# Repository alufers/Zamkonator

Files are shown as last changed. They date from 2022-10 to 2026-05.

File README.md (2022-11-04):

# Zamkonator - a PoE powered electronic lock system

**INFO**: This project is in a work in progress state and is not yet complete.

This is a repository for the hardware and software for a PoE powered locks system. It reads RFID cards using the [Wiegand interface](https://en.wikipedia.org/wiki/Wiegand_interface), and opens an electronic door latch to grant entry. This project simplifies the deployment of such systems by eliminating the need for a separate power supply for the lock. Additionally it connects directly to a LDAP server to authenticate users, thus removing any central coordination between multiple locks.

## Hardware overview

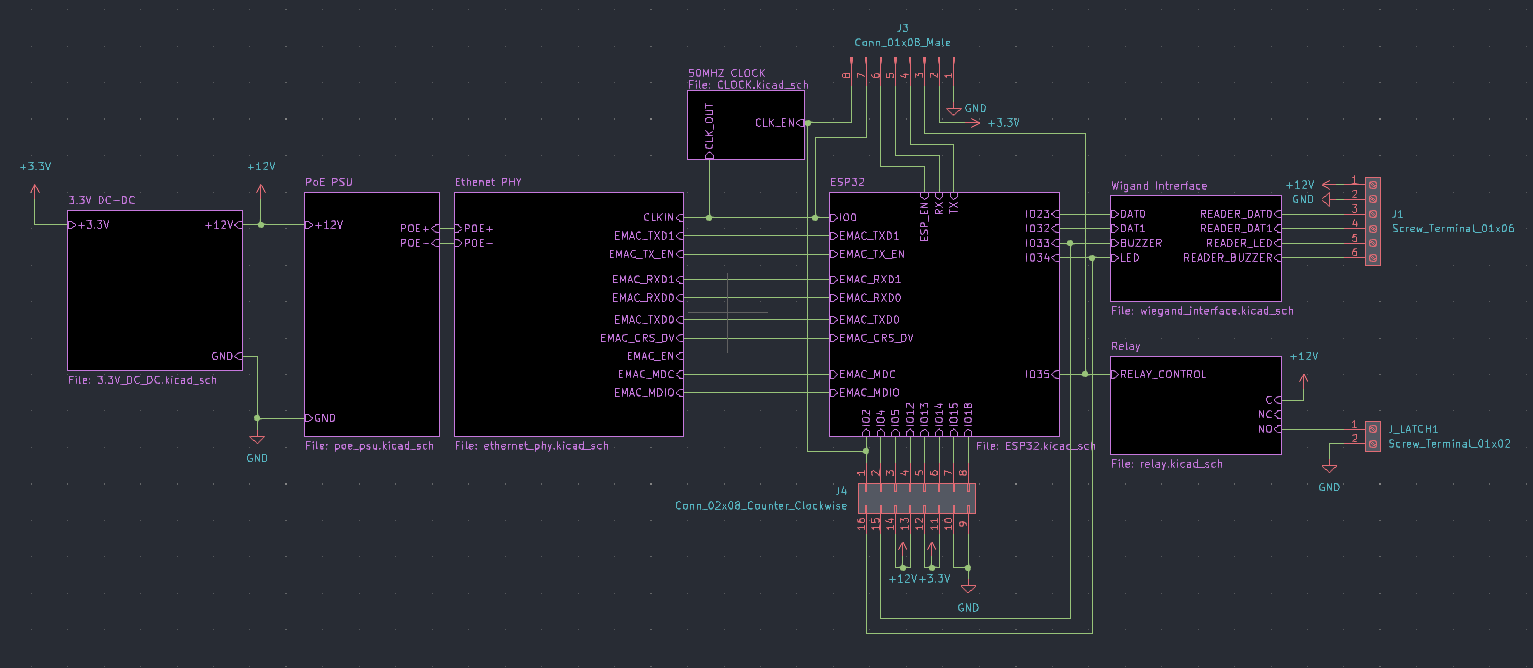
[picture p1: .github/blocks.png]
Hardware overview


The system is based on the ESP32 SoC and the RTL8201F PHY. The PoE power supply is supplied by the [SI3404-A-GM](https://datasheet.lcsc.com/lcsc/2108241830_SILICON-LABS-SI3404-A-GMR_C461934.pdf) IC. To provide an extra layer of safety, the Wiegand interface is isolated using optocouplers and the lock is controlled via a relay to eliminate any possibility of surges occuring in long cables.

[Full PDF schematic](./schematic.pdf)

## Firmware

The firmware is located in the `zamek-firmware/` directory. To build it you will need ESP-IDF 4.4.2.

### Building

```sh
# with the ESP-IDF activated, in the zamek-firmware/ directory
idf.py build
```

Alternatively you can use included nix shell, which automatically downloads and activates the ESP-IDF.

```sh
nix develop
idf.py build
```

### Flashing

```sh
# with the ESP-IDF activated
idf.py flash
```

If you are flashing a board for the first time you will also need to flash the littlefs partition. To do that run:

```sh
./flash_littlefs.sh
```

# License

MIT

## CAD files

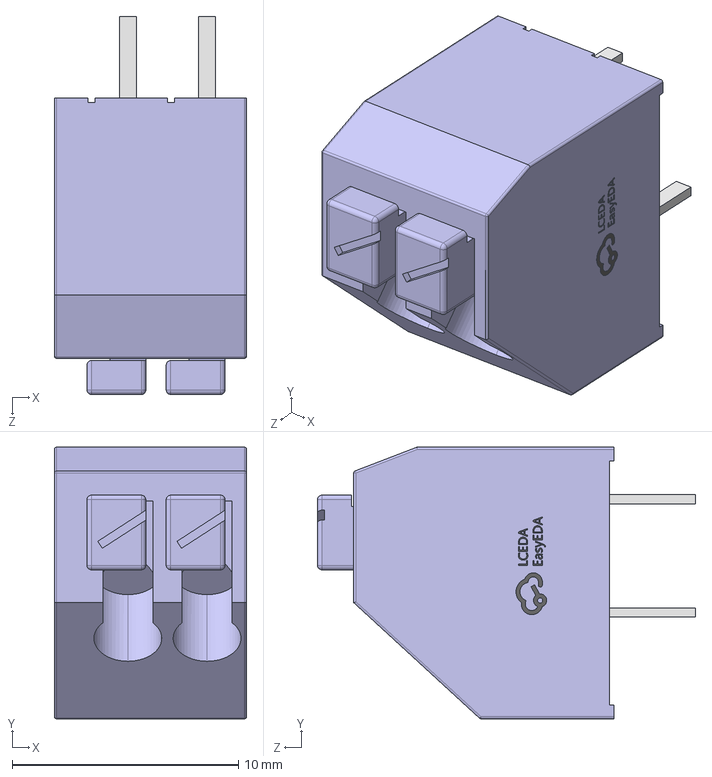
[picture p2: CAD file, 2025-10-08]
3d_models/CONN-TH_250-202.step
8.50 x 12.0 x 16.7 mm

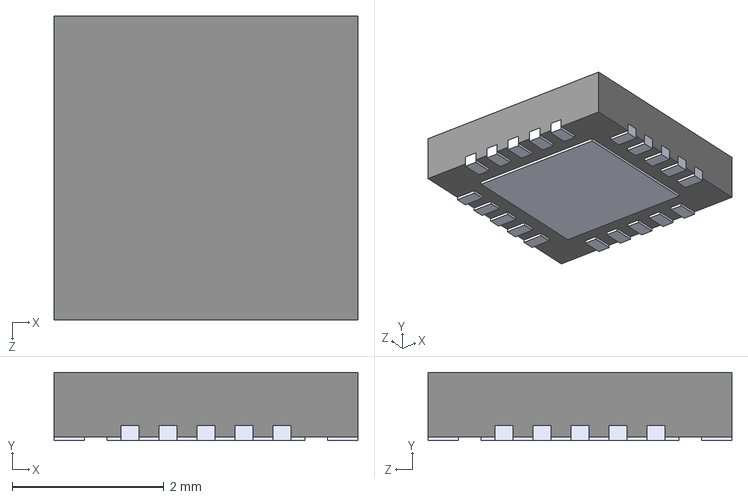
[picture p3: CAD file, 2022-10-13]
SI3404-A-GM.step
4.00 x 0.9 x 4.00 mm

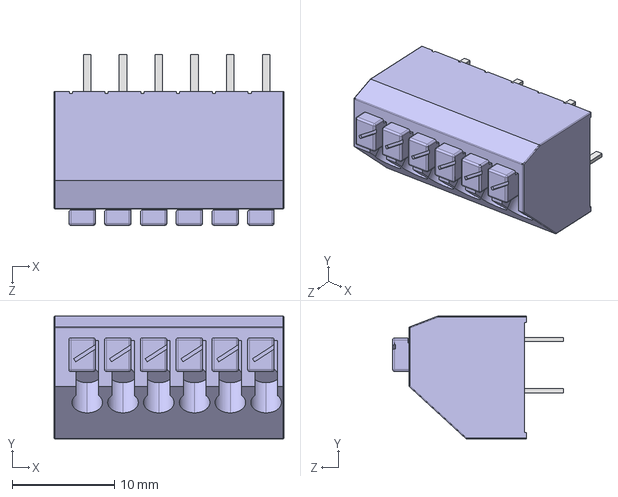
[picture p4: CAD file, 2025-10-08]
3d_models/CONN-TH_250-206.step
22.5 x 12.0 x 16.7 mm

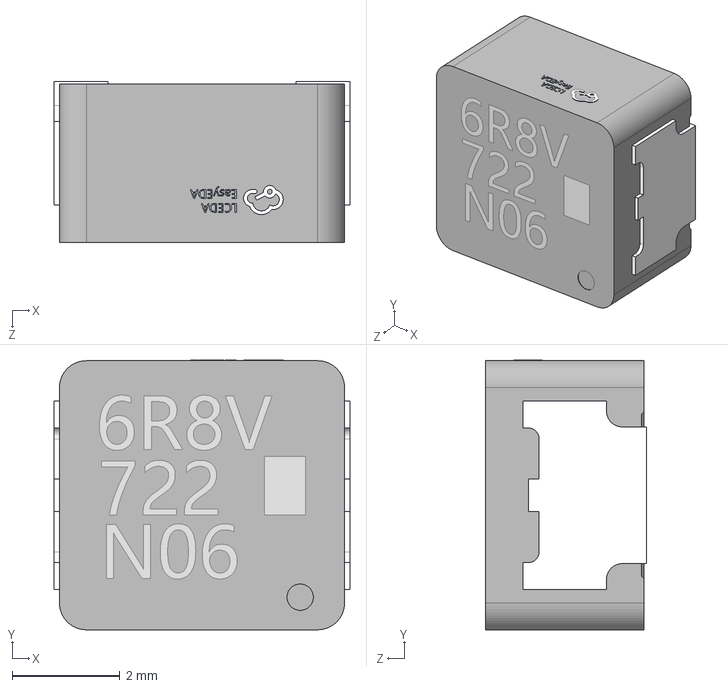
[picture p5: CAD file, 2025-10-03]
3d_models/IND-SMD_L5.5-W5.0-H3.0_ETQP4M220YFP.step
5.50 x 5.01 x 3.00 mm

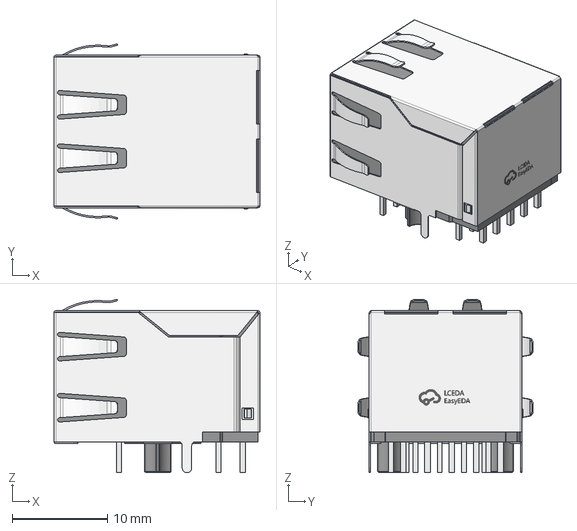
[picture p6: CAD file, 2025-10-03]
3d_models/RJ45-TH_HY931147C.step
21.6 x 18.4 x 18.2 mm

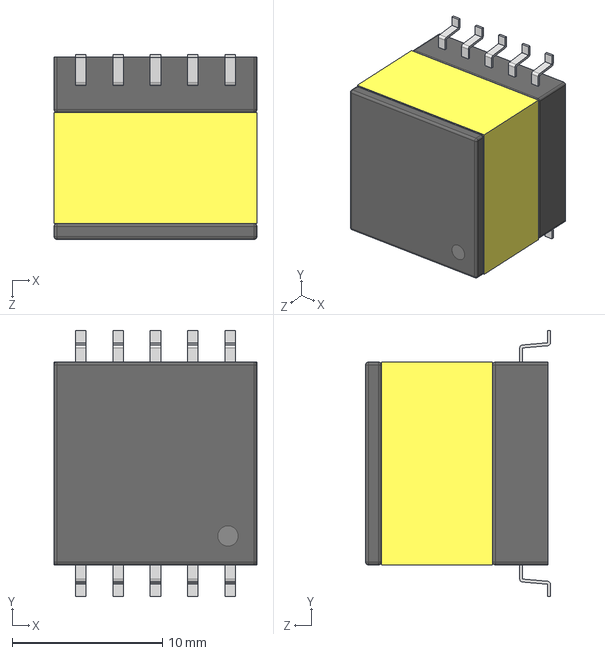
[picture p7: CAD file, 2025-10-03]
3d_models/XFMR-SMD_10P-L13.5-W13.5-H12.3-P2.48-LS17.7-BR.step
13.5 x 17.7 x 12.3 mm

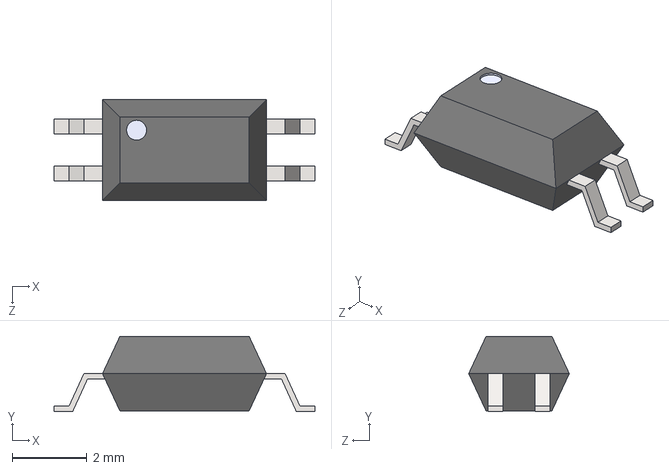
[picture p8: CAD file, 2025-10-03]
3d_models/SSOP-4.STEP
7.00 x 2.02 x 2.70 mm

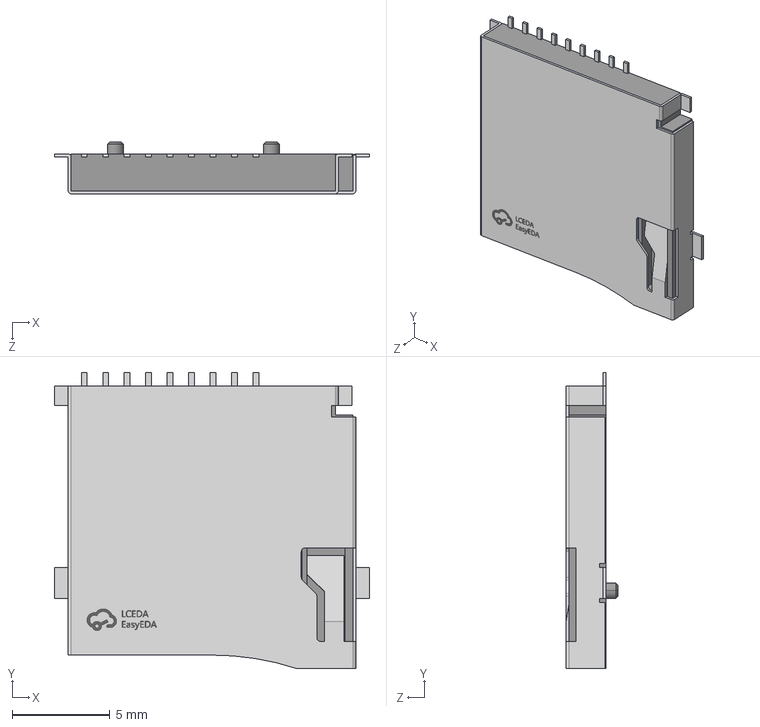
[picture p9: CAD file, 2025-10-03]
3d_models/TF-SMD_XKTF-N02-N.step
16.1 x 15.2 x 2.65 mm

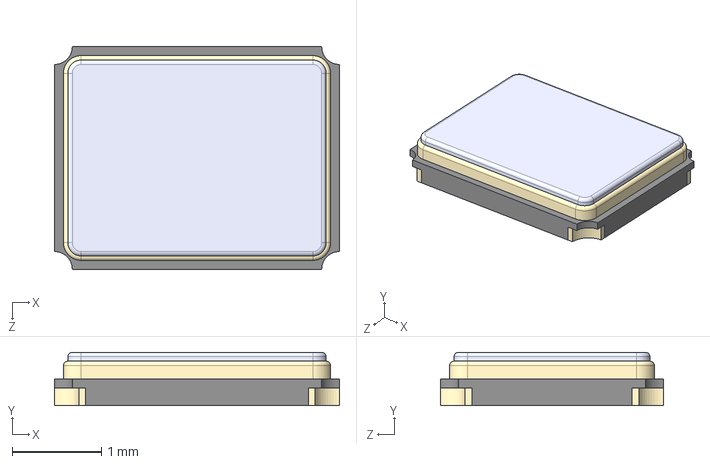
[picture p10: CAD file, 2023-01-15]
3d_models/Oscillator_3225.step
3.20 x 0.6 x 2.50 mm

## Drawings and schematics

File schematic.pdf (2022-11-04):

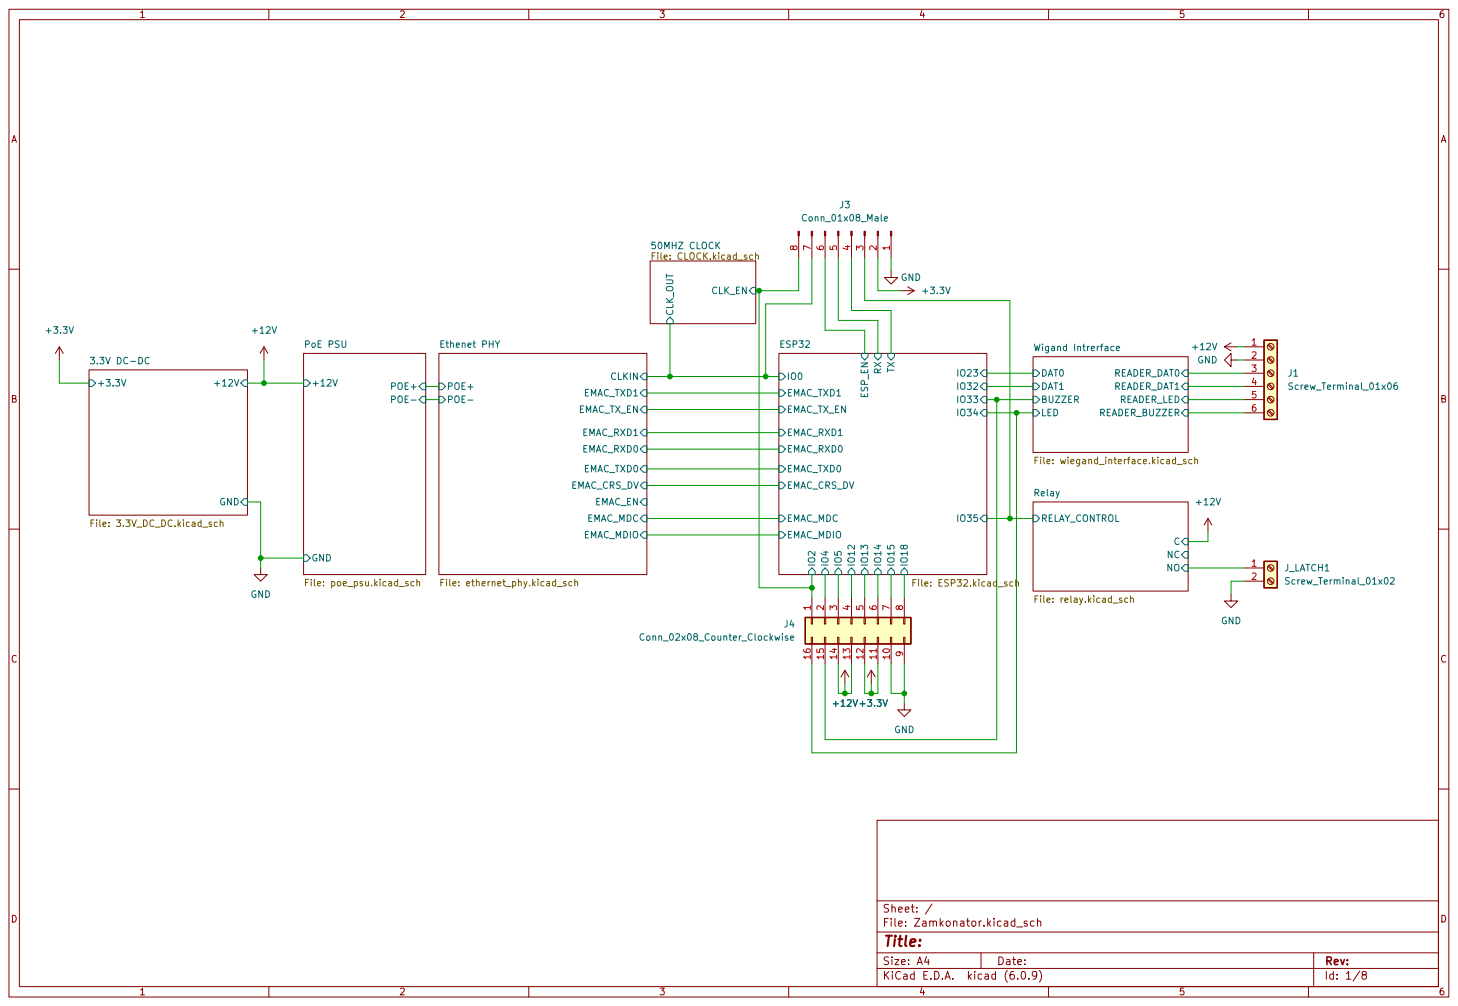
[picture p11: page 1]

POE+ POE- PoE PSU

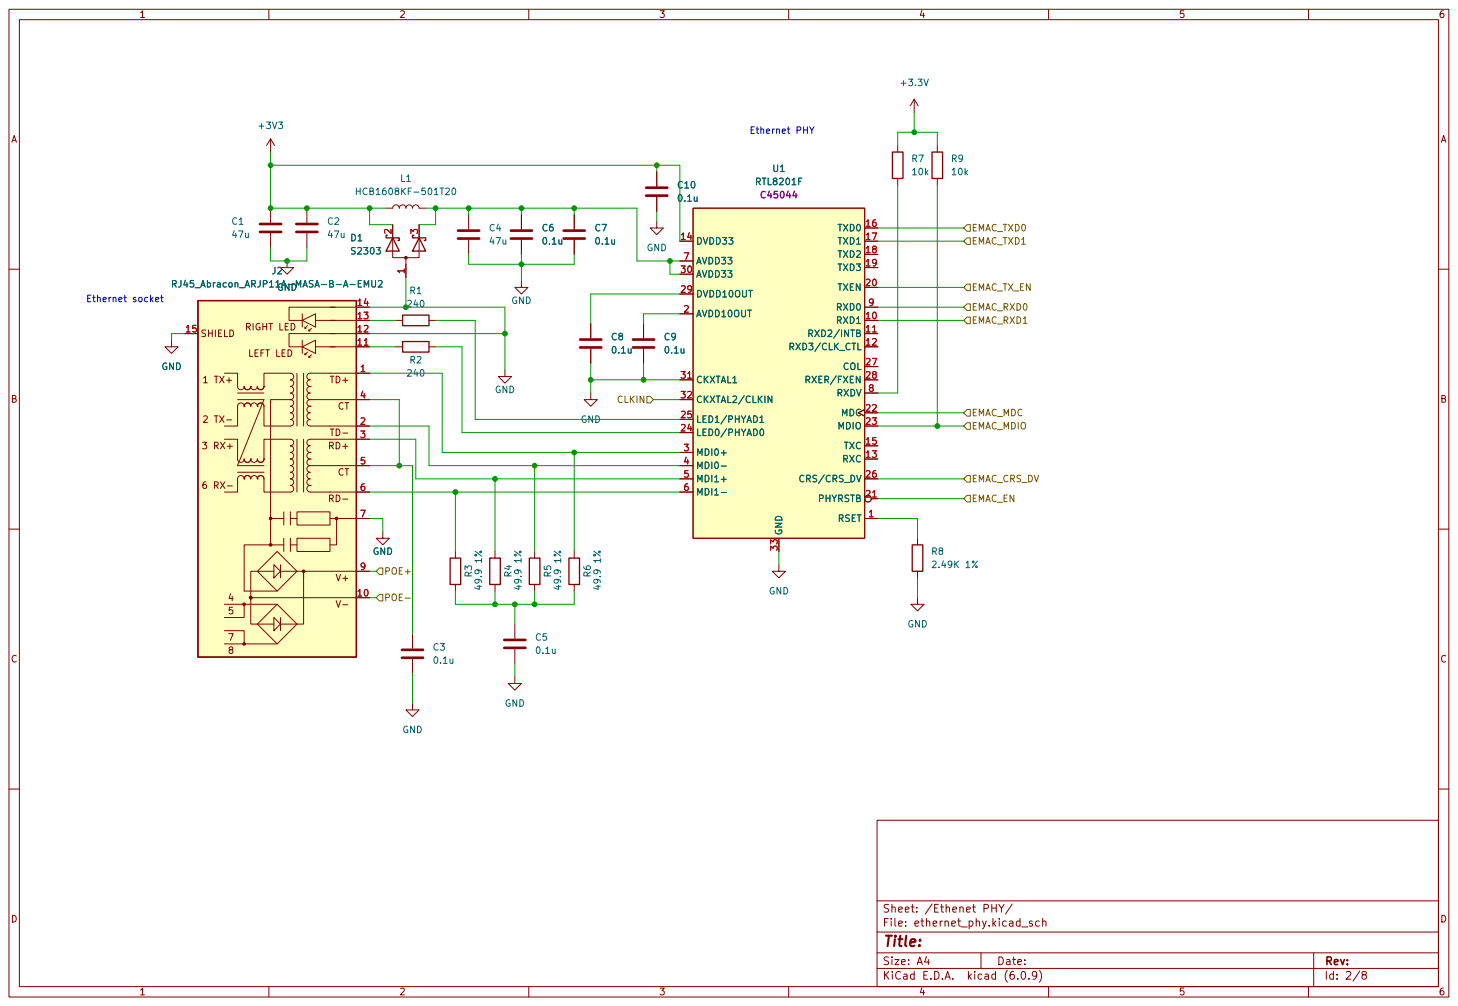
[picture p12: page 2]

Ethernet PHY
V+V- CT RD+ RIGHT LED

File: ethernet_phy.kicad_sch Sheet: /Ethenet PHY/
Id: 2/8 Title:

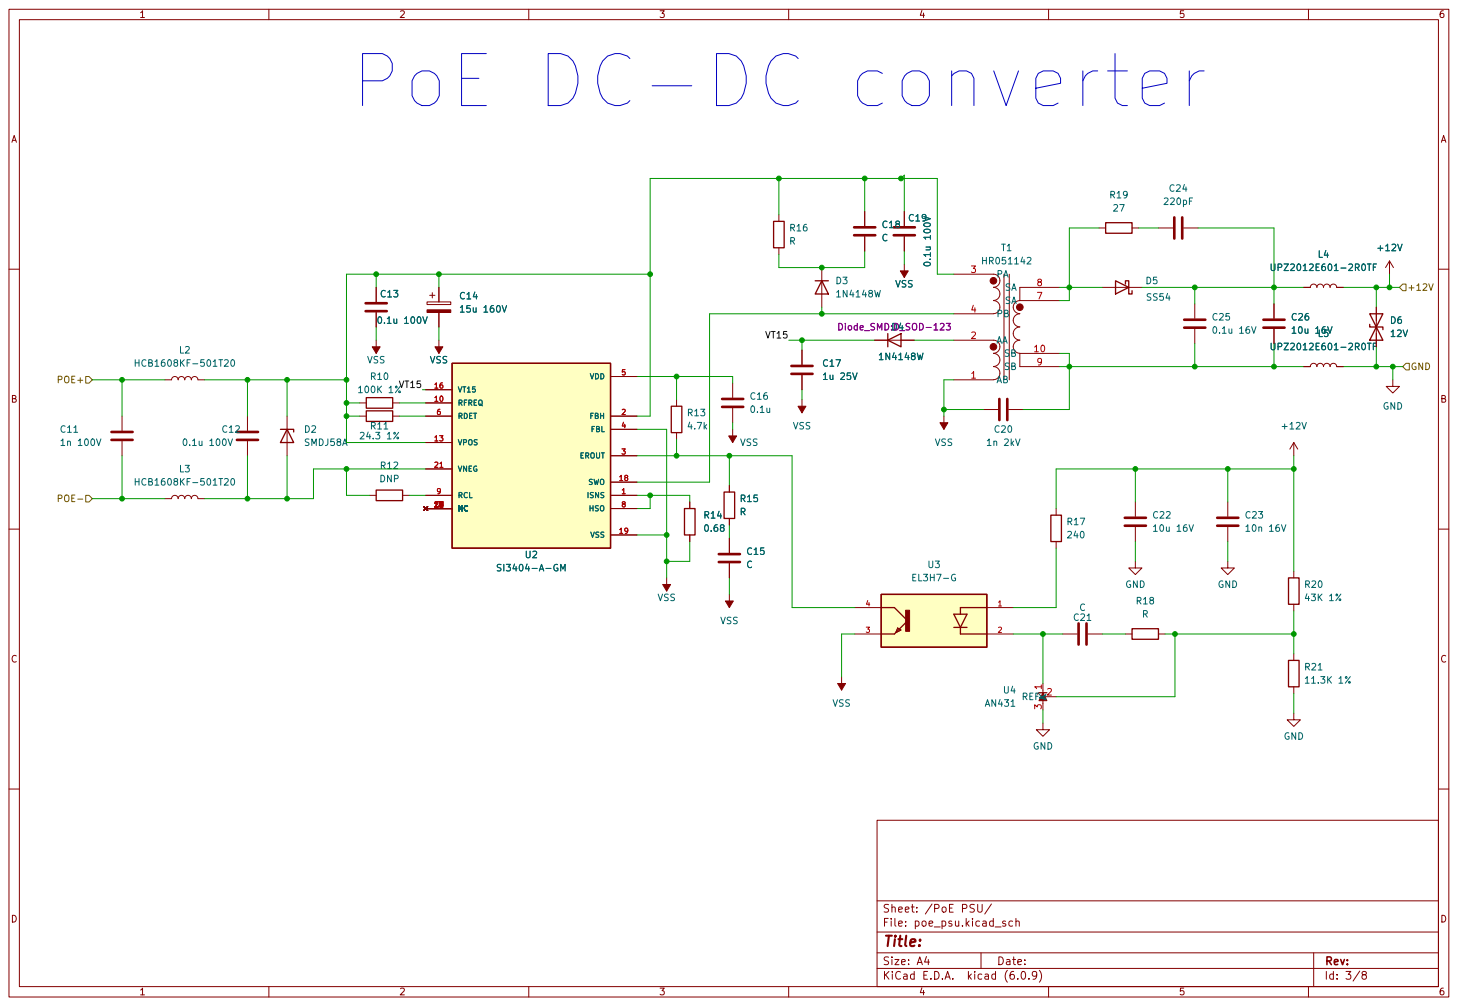
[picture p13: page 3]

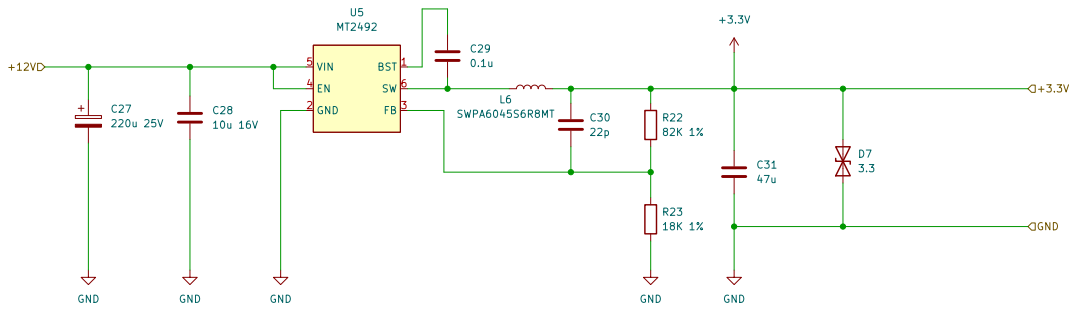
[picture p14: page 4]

File: 3.3V_DC_DC.kicad_sch Sheet: /3.3V DC-DC/
Id: 4/8 Title:

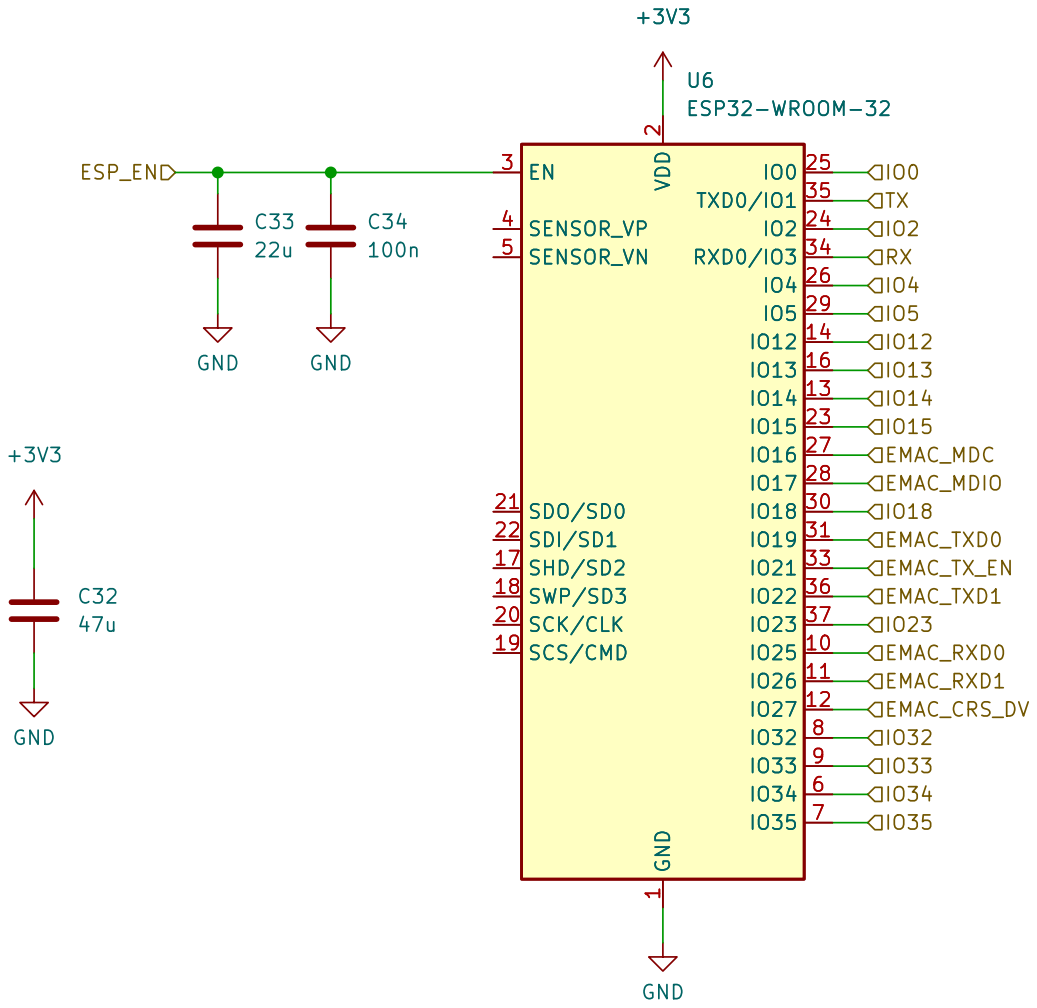
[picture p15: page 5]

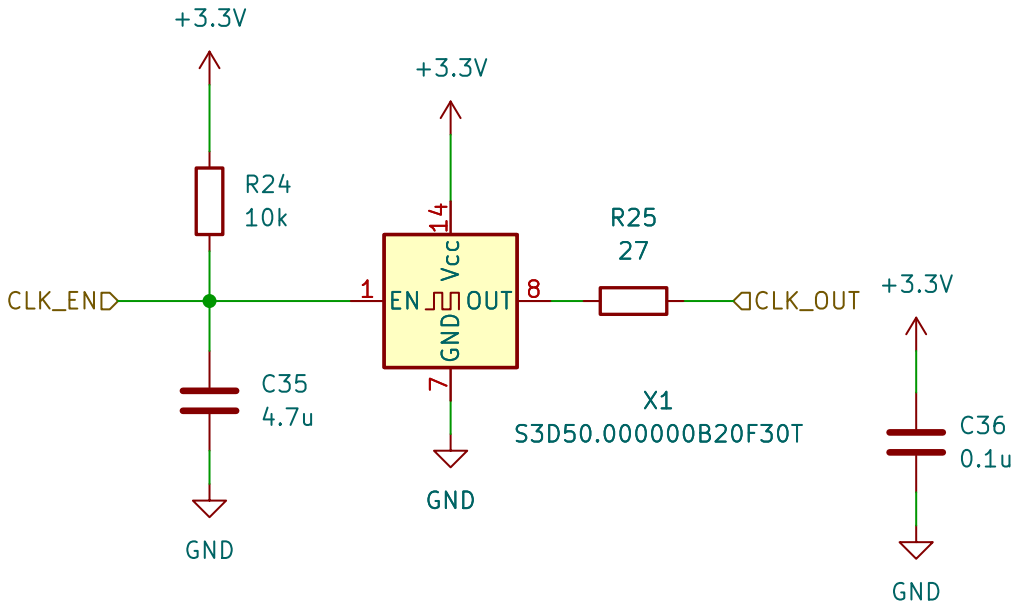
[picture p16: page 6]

File: CLOCK.kicad_sch Sheet: /50MHZ CLOCK/
Id: 6/8 Title:

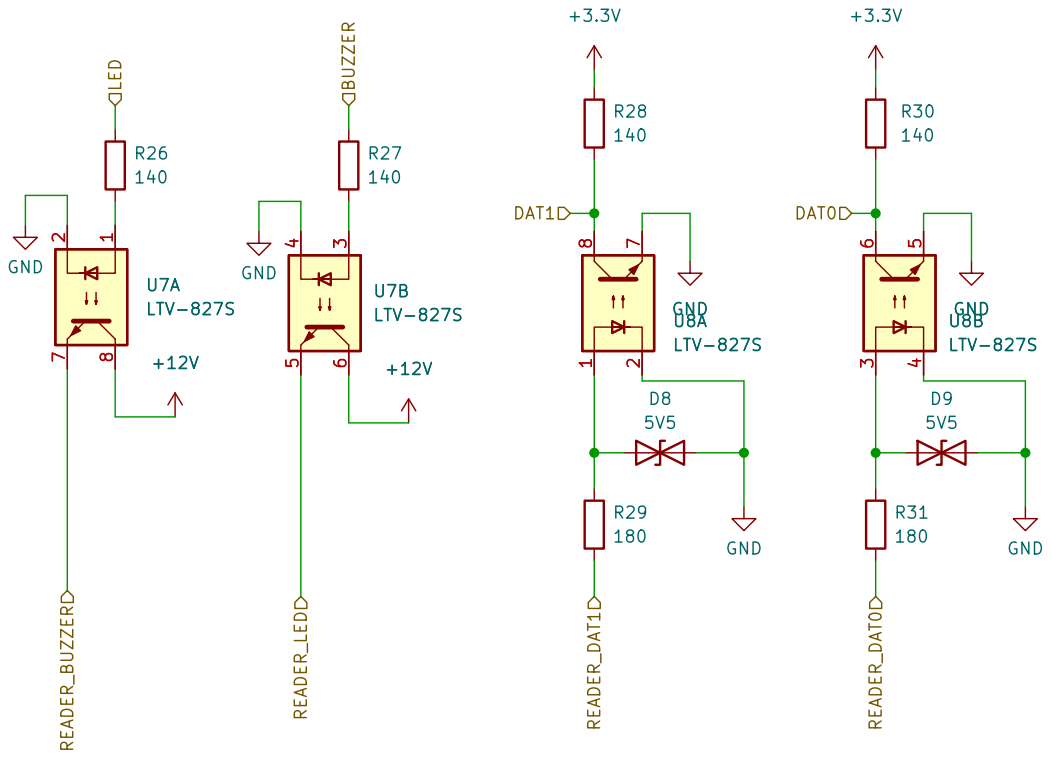
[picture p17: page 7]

Sheet: /Wigand Intrerface/ GND

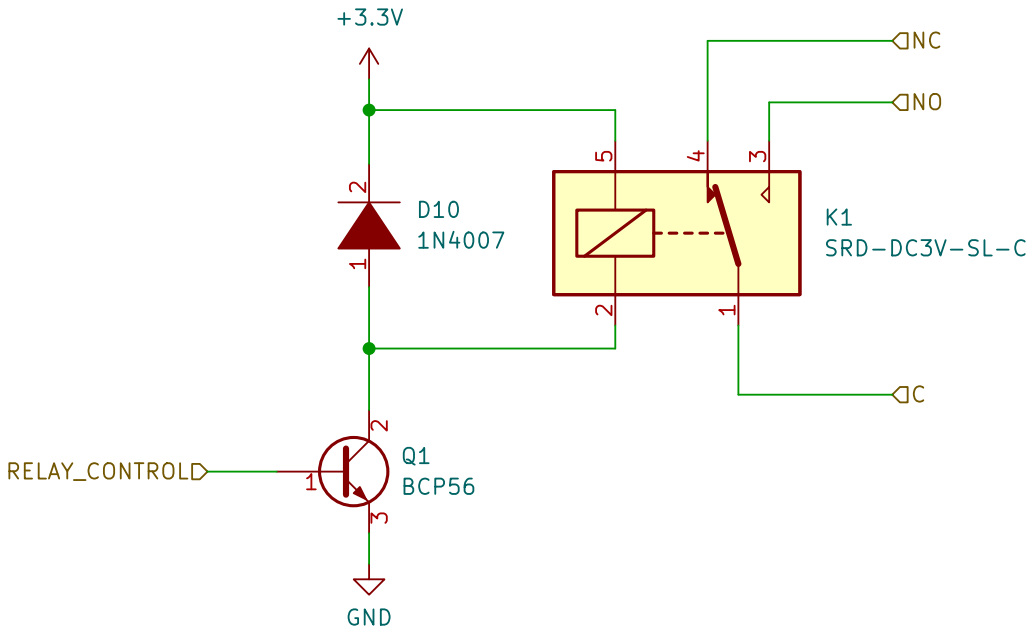
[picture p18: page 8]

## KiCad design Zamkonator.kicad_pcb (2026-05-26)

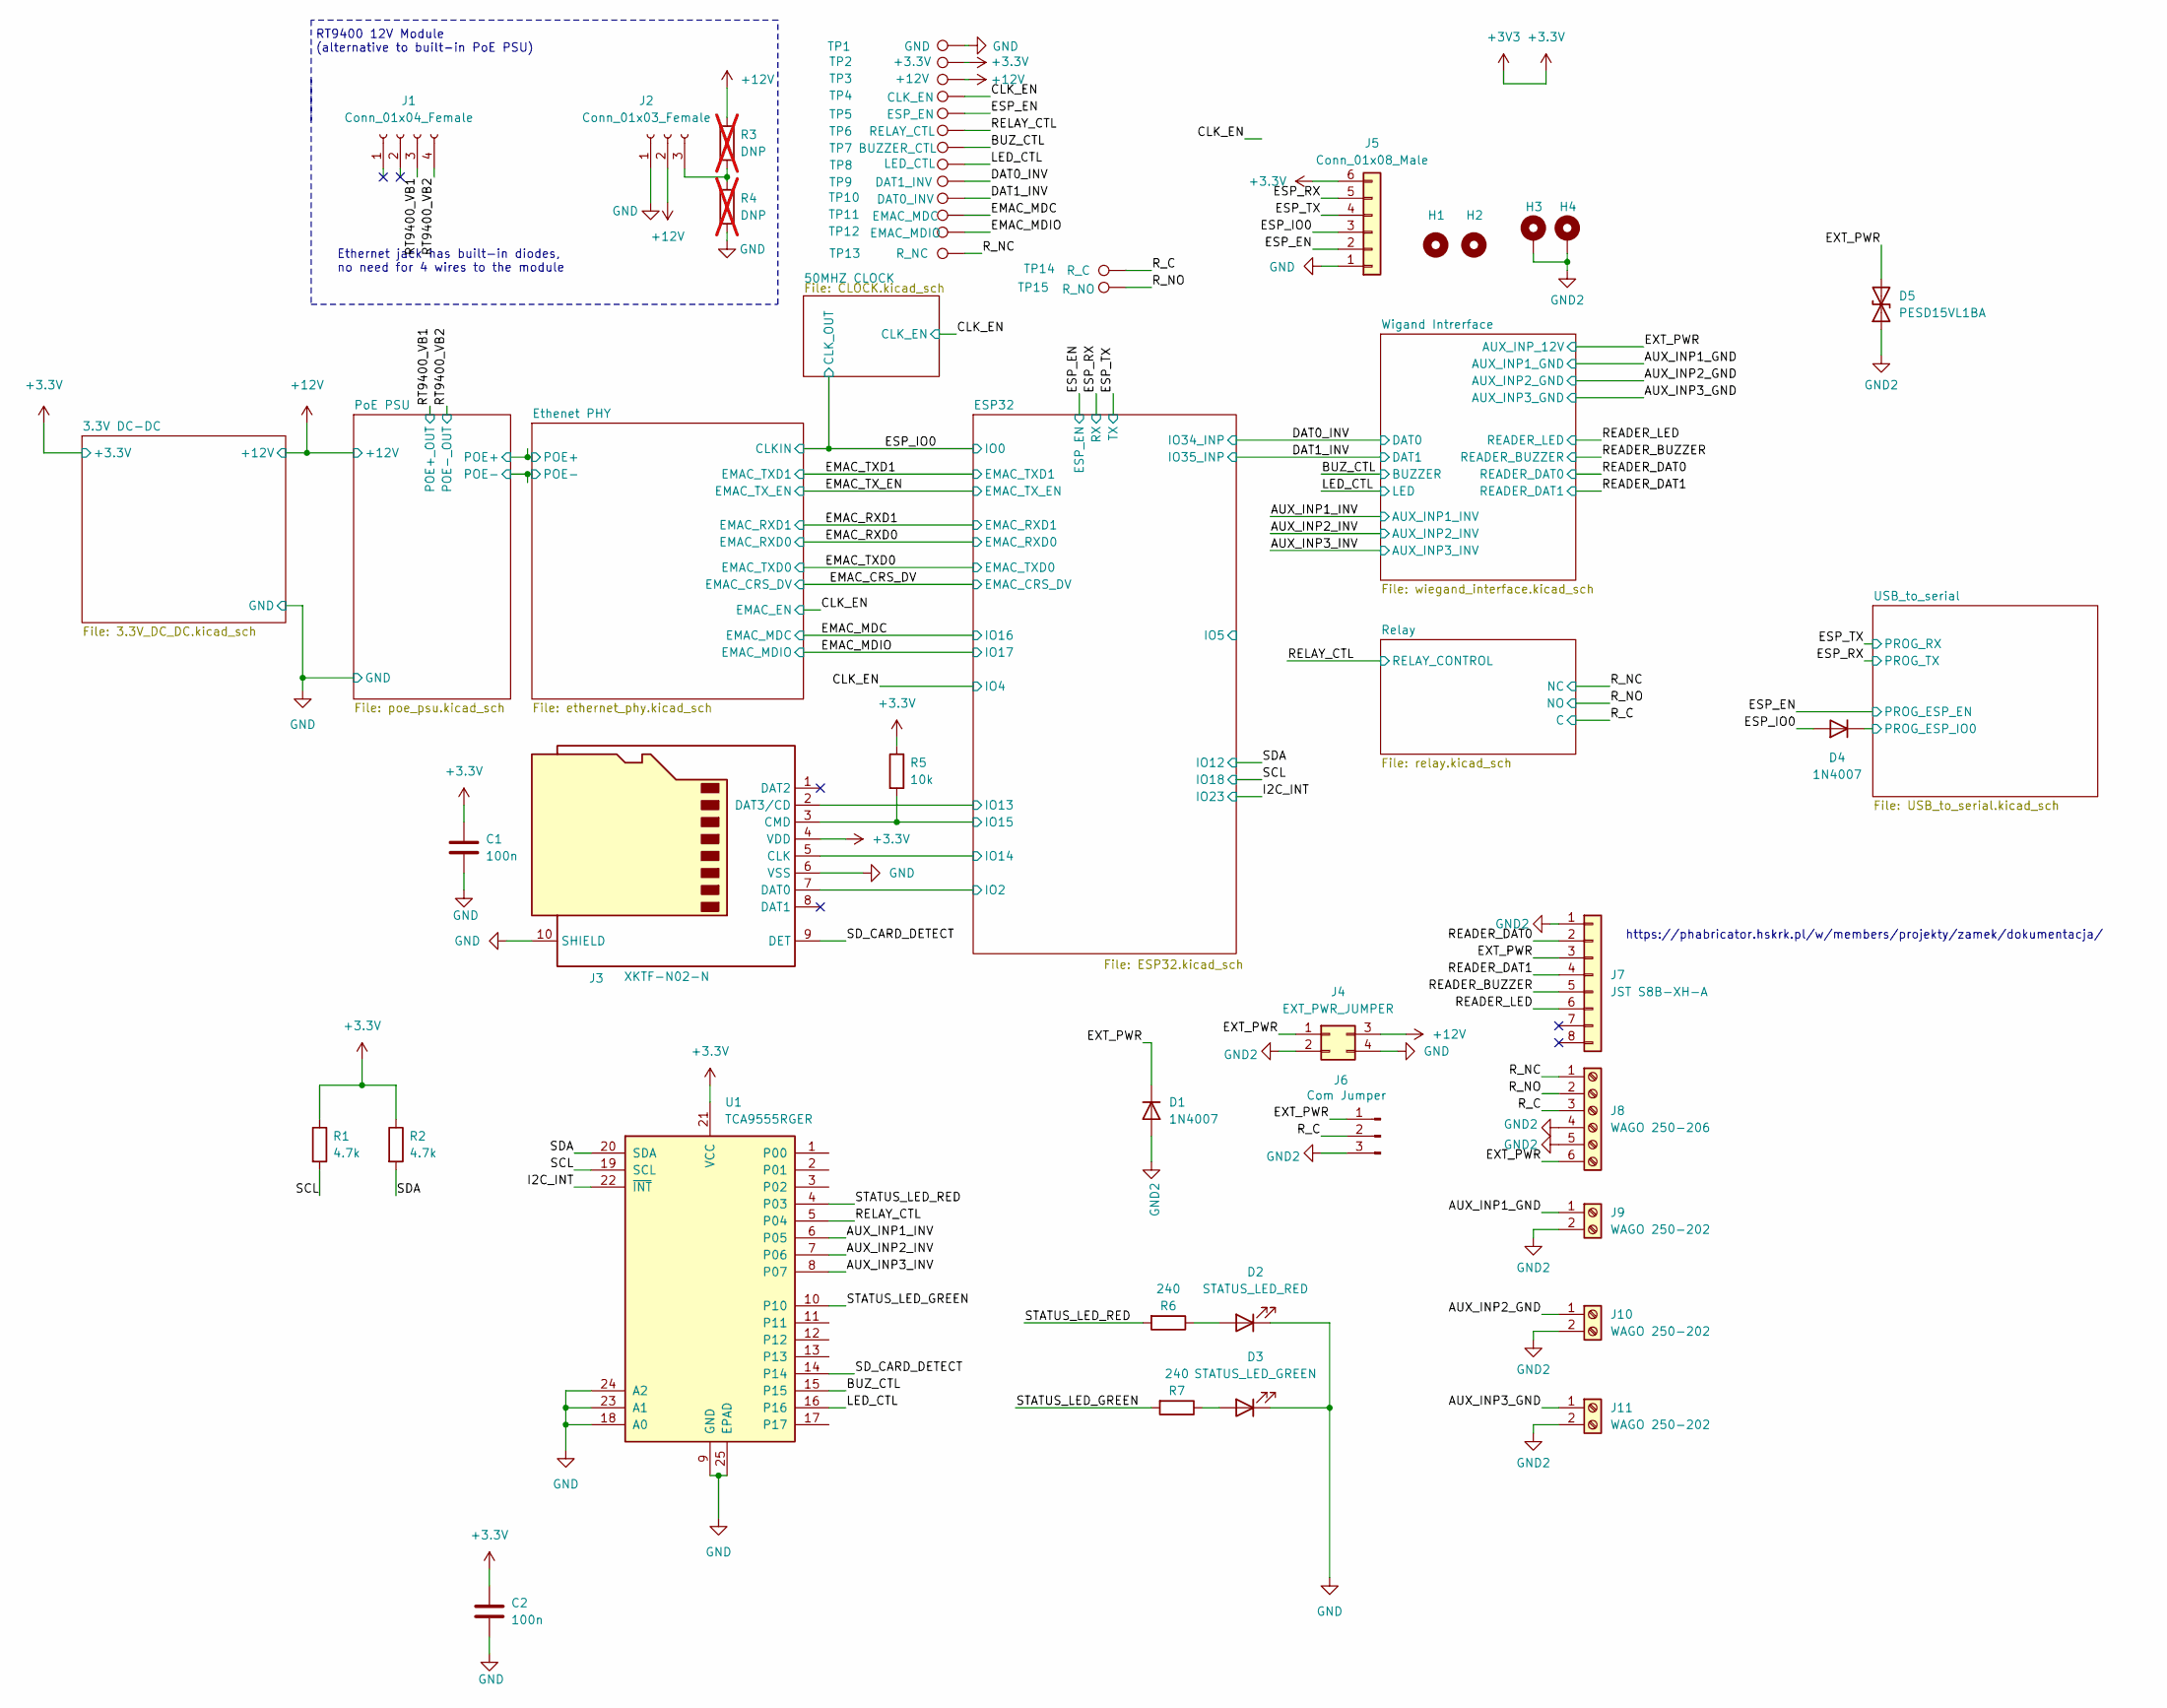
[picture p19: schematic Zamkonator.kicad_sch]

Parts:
C1, C2: 100n; C_0603_1608Metric_Pad1.08x0.95mm_HandSolder; LCSC C282519
D1, D4: 1N4007; D_SMA_Handsoldering; LCSC C7528875
D2: STATUS_LED_RED; LED_0603_1608Metric; LCSC C2286
D3: STATUS_LED_GREEN; LED_0603_1608Metric; LCSC C916074
D5: PESD15VL1BA; D_SOD-323; LCSC C18723438
H1, H2: MountingHole_Pad; MountingHole_3.2mm_M3
H3, H4: MountingHole_Pad; MountingHole_3.2mm_M3_Pad_Via
J1: Conn_01x04_Female; PinSocket_1x04_P2.54mm_Vertical; LCSC C2718488
J2: Conn_01x03_Female; PinSocket_1x03_P2.54mm_Vertical; LCSC C7509516
J3: XKTF-N02-N; TF-SMD_XKTF-N02-N; LCSC C381084
J4: EXT_PWR_JUMPER; PinHeader_2x02_P2.54mm_Vertical; LCSC C7501273
J5: Conn_01x08_Male; PinHeader_1x06_P2.54mm_Vertical; LCSC C37208
J6: Com Jumper; PinHeader_1x03_P2.54mm_Vertical; LCSC C2937625
J7: JST S8B-XH-A; JST_XH_S8B-XH-A_1x08_P2.50mm_Horizontal; LCSC C157914
J8: WAGO 250-206; CONN-TH_250-206; LCSC C7470120
J9, J10, J11: WAGO 250-202; CONN-TH_250-202; LCSC C5443567
R1, R2: 4.7k; R_0603_1608Metric_Pad0.98x0.95mm_HandSolder; LCSC C2907166
R3, R4: DNP; R_0603_1608Metric_Pad0.98x0.95mm_HandSolder; not fitted
R5: 10k; R_0603_1608Metric_Pad0.98x0.95mm_HandSolder; LCSC C2930027
R6, R7: 240; R_0603_1608Metric_Pad0.98x0.95mm_HandSolder; LCSC C2907130
TP1: GND; TestPoint_Pad_D3.0mm
TP2: +3.3V; TestPoint_Pad_D3.0mm
TP3: +12V; TestPoint_Pad_D3.0mm
TP4: CLK_EN; TestPoint_Pad_D1.5mm
TP5: ESP_EN; TestPoint_Pad_D1.5mm
TP6: RELAY_CTL; TestPoint_Pad_D1.5mm
TP7: BUZZER_CTL; TestPoint_Pad_D1.5mm
TP8: LED_CTL; TestPoint_Pad_D1.5mm
TP9: DAT1_INV; TestPoint_Pad_D1.5mm
TP10: DAT0_INV; TestPoint_Pad_D1.5mm
TP11: EMAC_MDC; TestPoint_Pad_D1.5mm
TP12: EMAC_MDIO; TestPoint_Pad_D1.5mm
TP13: R_NC; TestPoint_Pad_D3.0mm
TP14: R_C; TestPoint_Pad_D3.0mm
TP15: R_NO; TestPoint_Pad_D3.0mm
U1: TCA9555RGER; VQFN-24-1EP_4x4mm_P0.5mm_EP2.45x2.45mm; LCSC C42420609

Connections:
+3.3V: C1.1, C2.1, J3.4 (VDD), J5.6, R1.1, R2.1, R5.1, TP2.1 (1_1), U1.21 (VCC); also elsewhere on the board
+12V: J2.2, J4.3, R3.1, TP3.1 (1_1); also elsewhere on the board
/AUX_INP1_GND: J9.1; also elsewhere on the board
/AUX_INP1_INV: U1.6 (P05); also elsewhere on the board
/AUX_INP2_GND: J10.1; also elsewhere on the board
/AUX_INP2_INV: U1.7 (P06); also elsewhere on the board
/AUX_INP3_GND: J11.1; also elsewhere on the board
/AUX_INP3_INV: U1.8 (P07); also elsewhere on the board
/BUZ_CTL: TP7.1 (1_1), U1.15; also elsewhere on the board
/CLK_EN: TP4.1 (1_1); also elsewhere on the board
/DAT0_INV: TP9.1 (1_1); also elsewhere on the board
/DAT1_INV: TP10.1 (1_1); also elsewhere on the board
/EMAC_MDC: TP11.1 (1_1); also elsewhere on the board
/EMAC_MDIO: TP12.1 (1_1); also elsewhere on the board
/ESP32/IO2: J3.7 (DAT0); also elsewhere on the board
/ESP32/IO13: J3.2 (DAT3/CD); also elsewhere on the board
/ESP32/IO14: J3.5 (CLK); also elsewhere on the board
/ESP32/IO15: J3.3 (CMD), R5.2; also elsewhere on the board
/ESP_EN: J5.2, TP5.1 (1_1); also elsewhere on the board
/ESP_IO0: D4.2 (A), J5.3; also elsewhere on the board
/ESP_RX: J5.5; also elsewhere on the board
/ESP_TX: J5.4; also elsewhere on the board
/EXT_PWR: D1.1 (K), D5.2 (A2), J4.1, J6.1, J7.3, J8.6; also elsewhere on the board
/I2C_INT: U1.22 (~INT); also elsewhere on the board
/LED_CTL: TP8.1 (1_1), U1.16; also elsewhere on the board
/READER_BUZZER: J7.5; also elsewhere on the board
/READER_DAT0: J7.2; also elsewhere on the board
/READER_DAT1: J7.4; also elsewhere on the board
/READER_LED: J7.6; also elsewhere on the board
/RELAY_CTL: TP6.1 (1_1), U1.5 (P04); also elsewhere on the board
/RT9400_VB1: J1.3; also elsewhere on the board
/RT9400_VB2: J1.4; also elsewhere on the board
/R_C: J6.2, J8.3, TP14.1 (1_1); also elsewhere on the board
/R_NC: J8.1, TP13.1 (1_1); also elsewhere on the board
/R_NO: J8.2, TP15.1 (1_1); also elsewhere on the board
/SCL: R1.2, U1.19 (SCL); also elsewhere on the board
/SDA: R2.2, U1.20 (SDA); also elsewhere on the board
/SD_CARD_DETECT: J3.9 (DET), U1.14
/STATUS_LED_GREEN: R7.2, U1.10
/STATUS_LED_RED: R6.2, U1.4 (P03)
/USB_to_serial/PROG_ESP_IO0: D4.1 (K); also elsewhere on the board
GND: C1.2, C2.2, D2.1 (K), D3.1 (K), J2.1, J3.6 (VSS), J3.10 (SHIELD), J4.4, J5.1, R4.2, TP1.1 (1_1), U1.9 (GND), U1.18 (A0), U1.23 (A1), U1.24 (A2), U1.25 (EPAD); also elsewhere on the board
GND2: D1.2 (A), D5.1 (A1), H3.1 (1_1), H4.1 (1_1), J4.2, J6.3, J7.1, J8.4, J8.5, J9.2, J10.2, J11.2; also elsewhere on the board
unnamed: D2.2 (A), R6.1
unnamed: D3.2 (A), R7.1
unnamed: J2.3, R3.2, R4.1

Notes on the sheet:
RT9400 12V Module (alternative to built-in PoE PSU)
Ethernet jack has built-in diodes, no need for 4 wires to the module
https://phabricator.hskrk.pl/w/members/projekty/zamek/dokumentacja/

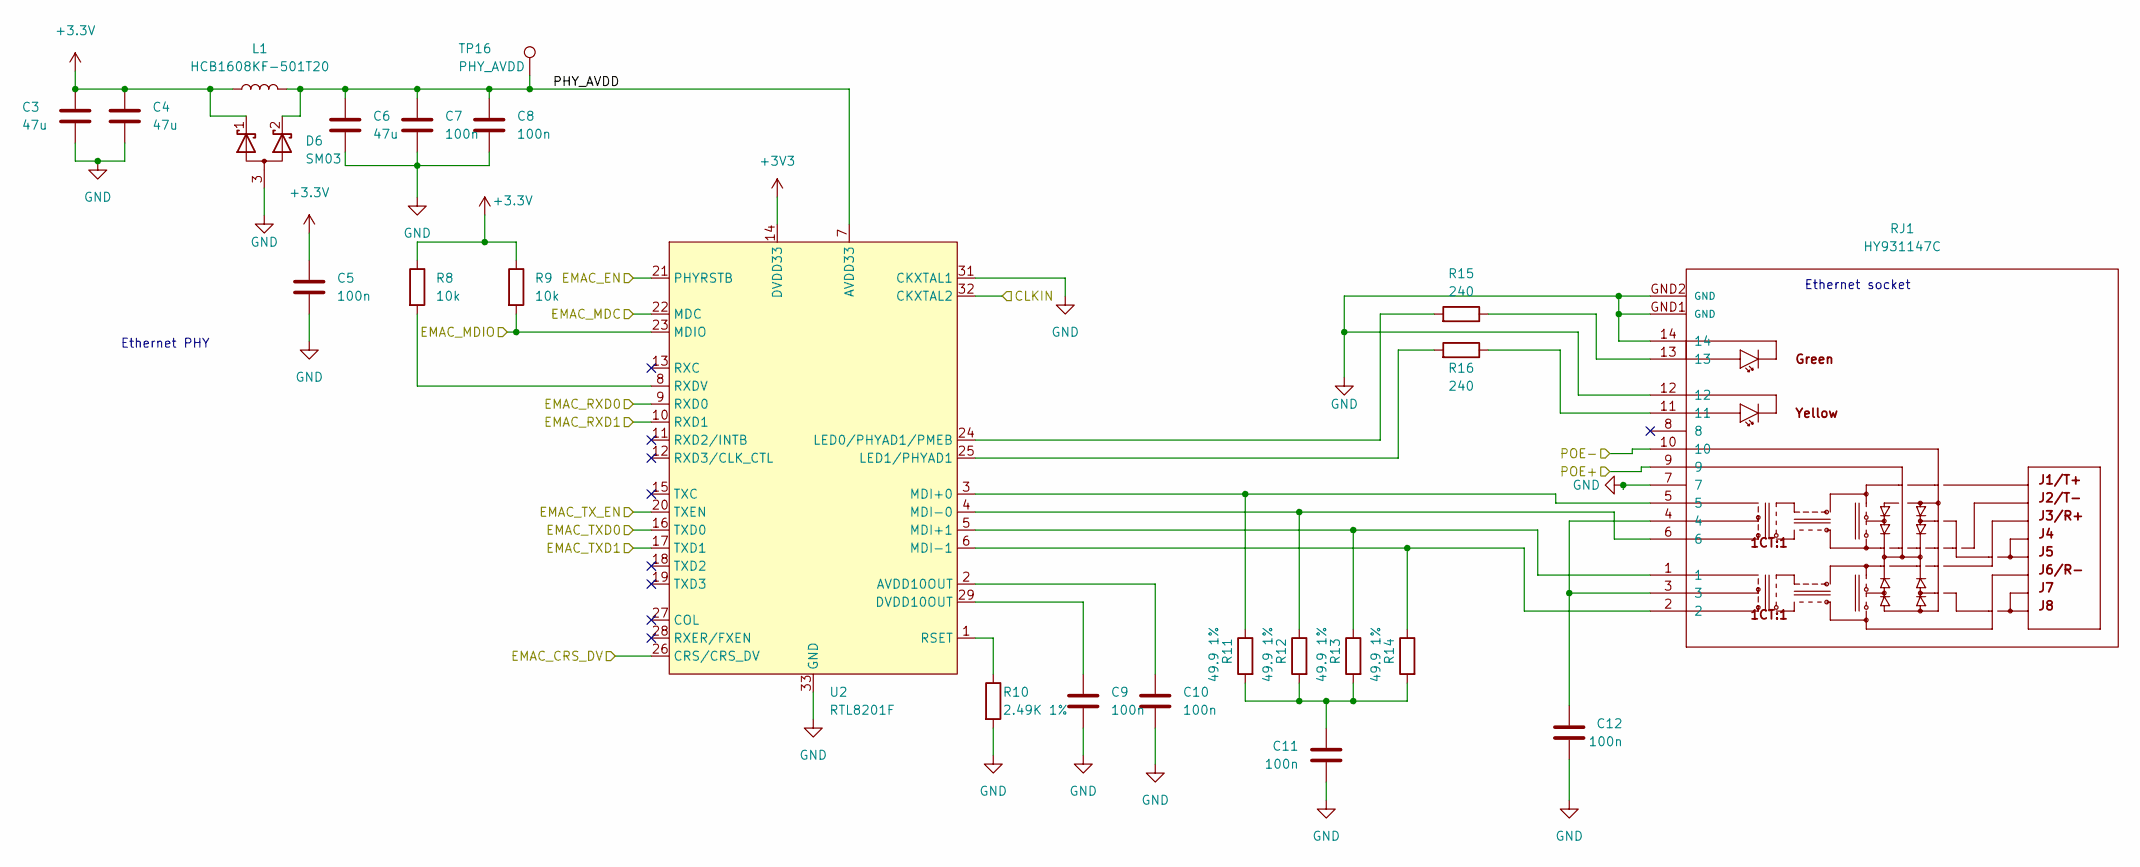
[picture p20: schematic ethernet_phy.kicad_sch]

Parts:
C3, C4, C6: 47u; C_0603_1608Metric_Pad1.08x0.95mm_HandSolder; LCSC C140782
C5, C7, C8, C9, C10, C11, C12: 100n; C_0603_1608Metric_Pad1.08x0.95mm_HandSolder; LCSC C282519
D6: SM03; TSOT-23_HandSoldering; LCSC C502558
L1: HCB1608KF-501T20; L_0603_1608Metric; LCSC C356979
R8, R9: 10k; R_0603_1608Metric_Pad0.98x0.95mm_HandSolder; LCSC C2930027
R10: 2.49K 1%; R_0603_1608Metric_Pad0.98x0.95mm_HandSolder; LCSC C100897
R11, R12, R13, R14: 49.9 1%; R_0603_1608Metric_Pad0.98x0.95mm_HandSolder; LCSC C114625
R15, R16: 240; R_0603_1608Metric_Pad0.98x0.95mm_HandSolder; LCSC C2907130
RJ1: HY931147C; RJ45-TH_HY931147C; LCSC C91754
TP16: PHY_AVDD; TestPoint_Pad_D1.5mm
U2: RTL8201F; QFN-32-1EP_5x5mm_P0.5mm_EP3.3x3.3mm; LCSC C45044

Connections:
+3.3V: C3.1, C4.1, C5.1, D6.1 (K), L1.1, R8.1, R9.1, U2.14 (DVDD33); also elsewhere on the board
/CLK_EN: U2.21 (PHYRSTB); also elsewhere on the board
/EMAC_CRS_DV: U2.26 (CRS/CRS_DV); also elsewhere on the board
/EMAC_MDC: U2.22 (MDC); also elsewhere on the board
/EMAC_MDIO: R9.2, U2.23 (MDIO); also elsewhere on the board
/EMAC_RXD0: U2.9 (RXD0); also elsewhere on the board
/EMAC_RXD1: U2.10 (RXD1); also elsewhere on the board
/EMAC_TXD0: U2.16 (TXD0); also elsewhere on the board
/EMAC_TXD1: U2.17 (TXD1); also elsewhere on the board
/EMAC_TX_EN: U2.20 (TXEN); also elsewhere on the board
/ESP_IO0: U2.32 (CKXTAL2); also elsewhere on the board
/Ethenet PHY/PHY_AVDD: C6.1, C7.1, C8.1, D6.2 (K), L1.2, TP16.1 (1_1), U2.7 (AVDD33), U2.30 (AVDD33)
/Ethenet PHY/POE+: RJ1.9; also elsewhere on the board
/Ethenet PHY/POE-: RJ1.10; also elsewhere on the board
GND: C3.2, C4.2, C5.2, C6.2, C7.2, C8.2, C9.2, C10.2, C11.2, C12.2, D6.3 (A), R10.2, RJ1.7, RJ1.12, RJ1.14, RJ1.GND1 (GND), RJ1.GND2 (GND), U2.31 (CKXTAL1), U2.33 (GND); also elsewhere on the board
unnamed: C11.1, R11.2, R12.2, R13.2, R14.2
unnamed: C12.1, RJ1.3, RJ1.4
unnamed: R15.1, RJ1.13
unnamed: R16.1, RJ1.11
unnamed: C10.1, U2.2 (AVDD10OUT)
unnamed: C9.1, U2.29 (DVDD10OUT)
unnamed: R15.2, U2.24 (LED0/PHYAD1/PMEB)
unnamed: R16.2, U2.25 (LED1/PHYAD1)
unnamed: R11.1, RJ1.5, U2.3 (MDI+0)
unnamed: R13.1, RJ1.1, U2.5 (MDI+1)
unnamed: R12.1, RJ1.6, U2.4 (MDI-0)
unnamed: R14.1, RJ1.2, U2.6 (MDI-1)
unnamed: R10.1, U2.1 (RSET)
unnamed: R8.2, U2.8 (RXDV)

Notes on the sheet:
Ethernet socket
Ethernet PHY

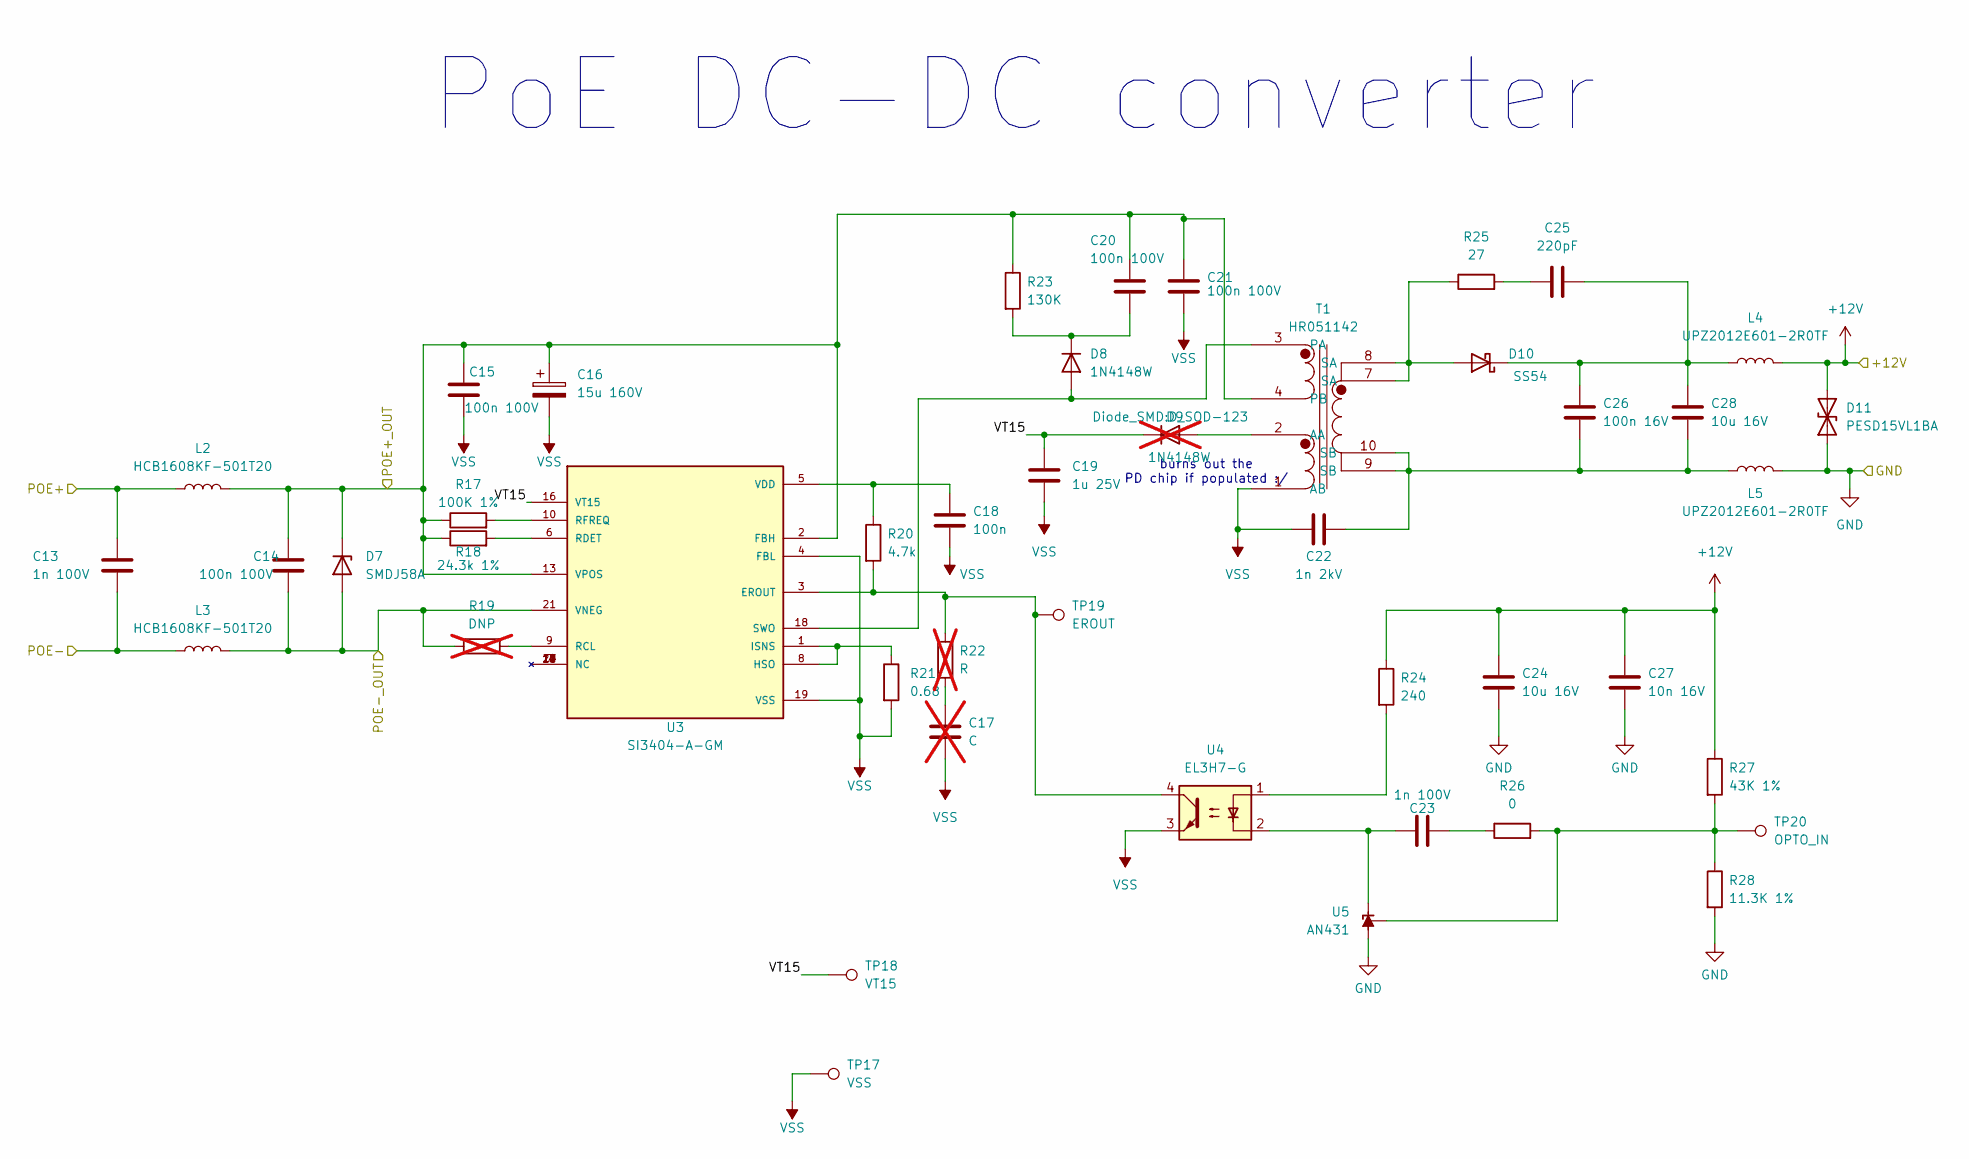
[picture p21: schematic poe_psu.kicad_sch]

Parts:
C13, C23: 1n 100V; C_0603_1608Metric_Pad1.08x0.95mm_HandSolder; LCSC C282513
C14, C15, C20, C21: 100n 100V; C_0603_1608Metric_Pad1.08x0.95mm_HandSolder; LCSC C696916
C16: 15u 160V; CP_Elec_10x10.5; LCSC C98557
C17: C; C_0603_1608Metric_Pad1.08x0.95mm_HandSolder; not fitted
C18: 100n; C_0603_1608Metric_Pad1.08x0.95mm_HandSolder; LCSC C282519
C19: 1u 25V; C_0603_1608Metric_Pad1.08x0.95mm_HandSolder; LCSC C5673
C22: 1n 2kV; C_1206_3216Metric_Pad1.33x1.80mm_HandSolder; LCSC C363565
C24, C28: 10u 16V; C_0603_1608Metric_Pad1.08x0.95mm_HandSolder; LCSC C92487
C25: 220pF; C_0603_1608Metric_Pad1.08x0.95mm_HandSolder; LCSC C2760542
C26: 100n 16V; C_0603_1608Metric_Pad1.08x0.95mm_HandSolder; LCSC C696916
C27: 10n 16V; C_0603_1608Metric_Pad1.08x0.95mm_HandSolder; LCSC C163173
D7: SMDJ58A; D_SMB-SMC_Universal_Handsoldering; LCSC C4154735
D8: 1N4148W; D_SOD-123; LCSC C444720
D9: 1N4148W; D_SOD-123; LCSC C181133; not fitted
D10: SS54; D_SMA_Handsoldering; LCSC C513478
D11: PESD15VL1BA; D_SOD-323; LCSC C18723438
L2, L3: HCB1608KF-501T20; L_0603_1608Metric; LCSC C356979
L4, L5: UPZ2012E601-2R0TF; L_0805_2012Metric_Pad1.15x1.40mm_HandSolder; LCSC C98308
R17: 100K 1%; R_0603_1608Metric_Pad0.98x0.95mm_HandSolder; LCSC C2906980
R18: 24.3k 1%; R_0603_1608Metric_Pad0.98x0.95mm_HandSolder; LCSC C276290
R19: DNP; R_0603_1608Metric_Pad0.98x0.95mm_HandSolder; not fitted
R20: 4.7k; R_0603_1608Metric_Pad0.98x0.95mm_HandSolder; LCSC C2907166
R21: 0.68; R_0603_1608Metric_Pad0.98x0.95mm_HandSolder; LCSC C5126107
R22: R; R_0603_1608Metric_Pad0.98x0.95mm_HandSolder; not fitted
R23: 130K; R_0603_1608Metric_Pad0.98x0.95mm_HandSolder; LCSC C2906991
R24: 240; R_0603_1608Metric_Pad0.98x0.95mm_HandSolder; LCSC C2907130
R25: 27; R_0603_1608Metric_Pad0.98x0.95mm_HandSolder; LCSC C5140675
R26: 0; R_0603_1608Metric_Pad0.98x0.95mm_HandSolder; LCSC C100044
R27: 43K 1%; R_0603_1608Metric_Pad0.98x0.95mm_HandSolder; LCSC C137719
R28: 11.3K 1%; R_0603_1608Metric_Pad0.98x0.95mm_HandSolder; LCSC C137803
T1: HR051142; LCSC C55680
TP17: VSS; TestPoint_Pad_D1.5mm
TP18: VT15; TestPoint_Pad_D1.5mm
TP19: EROUT; TestPoint_Pad_D1.5mm
TP20: OPTO_IN; TestPoint_Pad_D1.5mm
U3: SI3404-A-GM; MLF-20-1EP_4x4mm_P0.5mm_EP2.6x2.6mm_ThermalVias; PARTREV 1.0; LCSC C461934
U4: EL3H7-G; SSOP-4_4.4x2.6mm_P1.27mm; LCSC C92243
U5: AN431; SOT-23; LCSC C97717

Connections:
+12V: C24.1, C27.1, D11.2 (A2), L4.2, R24.1, R27.1; also elsewhere on the board
/Ethenet PHY/POE+: C13.1, L2.1; also elsewhere on the board
/Ethenet PHY/POE-: C13.2, L3.1; also elsewhere on the board
/PoE PSU/VT15: C19.1, D9.1 (K), TP18.1 (1_1), U3.16 (VT15)
/RT9400_VB1: C14.1, C15.1, C16.1, C20.1, C21.1, D7.1 (K), L2.2, R17.1, R18.1, R23.1, T1.4 (PB), U3.2 (FBH), U3.13 (VPOS); also elsewhere on the board
/RT9400_VB2: C14.2, D7.2 (A), L3.2, R19.1, U3.21 (VNEG); also elsewhere on the board
GND: C24.2, C27.2, D11.1 (A1), L5.2, R28.2, U5.3 (A); also elsewhere on the board
unnamed: C17.1, R22.2
unnamed: C22.2, C26.2, C28.2, L5.1, T1.9 (SB), T1.10 (SB)
unnamed: C23.2, R26.1
unnamed: C25.1, R25.2
unnamed: D8.2 (A), T1.3 (PA), U3.18 (SWO)
unnamed: C20.2, D8.1 (K), R23.2
unnamed: D9.2 (A), T1.2 (AA)
unnamed: D10.2 (A), R25.1, T1.7 (SA), T1.8 (SA)
unnamed: C25.2, C26.1, C28.1, D10.1 (K), L4.1
unnamed: R24.2, U4.1
unnamed: R20.2, R22.1, TP19.1 (1_1), U3.3 (EROUT), U4.4
unnamed: R21.1, U3.1 (ISNS), U3.8 (HSO)
unnamed: R19.2, U3.9 (RCL)
unnamed: R18.2, U3.6 (RDET)
unnamed: R17.2, U3.10 (RFREQ)
unnamed: C18.1, R20.1, U3.5 (VDD)
unnamed: C23.1, U4.2, U5.1 (K)
unnamed: R26.2, R27.2, R28.1, TP20.1 (1_1), U5.2 (REF)
VSS: C15.2, C16.2, C17.2, C18.2, C19.2, C21.2, C22.1, R21.2, T1.1 (AB), TP17.1 (1_1), U3.4 (FBL), U3.19 (VSS), U4.3

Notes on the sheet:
PoE DC-DC converter
burns out the PD chip if populated :/

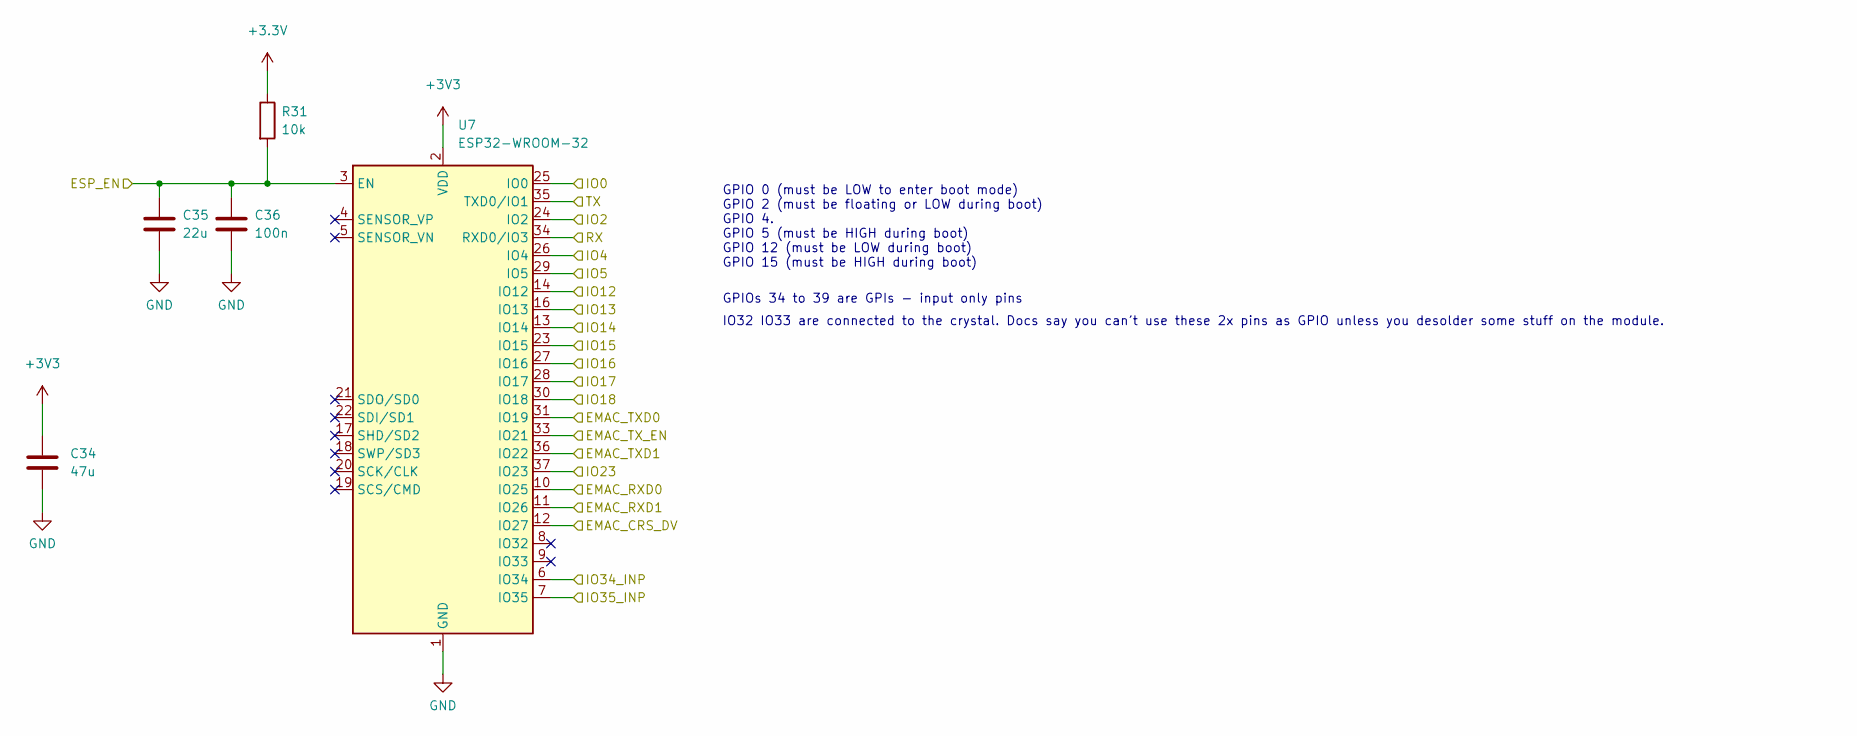
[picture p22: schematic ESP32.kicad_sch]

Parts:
C34: 47u; C_0603_1608Metric_Pad1.08x0.95mm_HandSolder; LCSC C140782
C35: 22u; C_0603_1608Metric_Pad1.08x0.95mm_HandSolder; LCSC C59461
C36: 100n; C_0603_1608Metric_Pad1.08x0.95mm_HandSolder; LCSC C282519
R31: 10k; R_0603_1608Metric_Pad0.98x0.95mm_HandSolder; LCSC C2930027
U7: ESP32-WROOM-32; LCSC C473012

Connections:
+3.3V: C34.1, R31.1, U7.2 (VDD); also elsewhere on the board
/CLK_EN: U7.26 (IO4); also elsewhere on the board
/DAT0_INV: U7.6 (IO34); also elsewhere on the board
/DAT1_INV: U7.7 (IO35); also elsewhere on the board
/EMAC_CRS_DV: U7.12 (IO27); also elsewhere on the board
/EMAC_MDC: U7.27 (IO16); also elsewhere on the board
/EMAC_MDIO: U7.28 (IO17); also elsewhere on the board
/EMAC_RXD0: U7.10 (IO25); also elsewhere on the board
/EMAC_RXD1: U7.11 (IO26); also elsewhere on the board
/EMAC_TXD0: U7.31 (IO19); also elsewhere on the board
/EMAC_TXD1: U7.36 (IO22); also elsewhere on the board
/EMAC_TX_EN: U7.33 (IO21); also elsewhere on the board
/ESP32/IO2: U7.24 (IO2); also elsewhere on the board
/ESP32/IO5: U7.29 (IO5)
/ESP32/IO13: U7.16 (IO13); also elsewhere on the board
/ESP32/IO14: U7.13 (IO14); also elsewhere on the board
/ESP32/IO15: U7.23 (IO15); also elsewhere on the board
/ESP_EN: C35.1, C36.1, R31.2, U7.3 (EN); also elsewhere on the board
/ESP_IO0: U7.25 (IO0); also elsewhere on the board
/ESP_RX: U7.34 (RXD0/IO3); also elsewhere on the board
/ESP_TX: U7.35 (TXD0/IO1); also elsewhere on the board
/I2C_INT: U7.37 (IO23); also elsewhere on the board
/SCL: U7.30 (IO18); also elsewhere on the board
/SDA: U7.14 (IO12); also elsewhere on the board
GND: C34.2, C35.2, C36.2, U7.1 (GND), U7.15 (GND), U7.38 (GND), U7.39 (GND); also elsewhere on the board

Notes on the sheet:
IO32 IO33 are connected to the crystal. Docs say you can't use these 2x pins as GPIO unless you desolder some stuff on the module.
GPIOs 34 to 39 are GPIs - input only pins
GPIO 0 (must be LOW to enter boot mode) GPIO 2 (must be floating or LOW during boot) GPIO 4. GPIO 5 (must be HIGH during boot) GPIO 12 (must be LOW during boot) GPIO 15 (must be HIGH during boot)

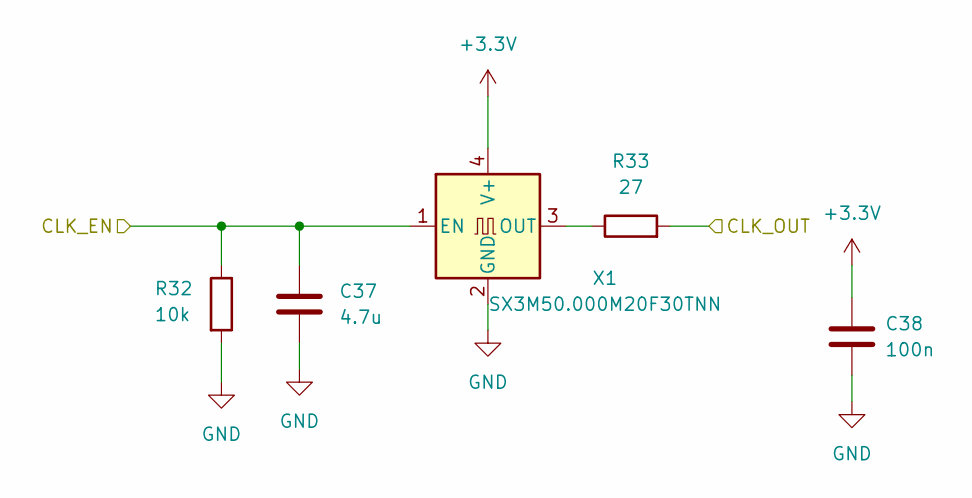
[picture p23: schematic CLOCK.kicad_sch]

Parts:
C37: 4.7u; C_0603_1608Metric_Pad1.08x0.95mm_HandSolder; LCSC C8032
C38: 100n; C_0603_1608Metric_Pad1.08x0.95mm_HandSolder; LCSC C282519
R32: 10k; R_0603_1608Metric_Pad0.98x0.95mm_HandSolder; LCSC C2930027
R33: 27; R_0603_1608Metric_Pad0.98x0.95mm_HandSolder; LCSC C5140675
X1: SX3M50.000M20F30TNN; Oscillator_SMD_EuroQuartz_XO32-4Pin_3.2x2.5mm; LCSC C2901592

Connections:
+3.3V: C38.1, X1.4 (V+); also elsewhere on the board
/CLK_EN: C37.1, R32.1, X1.1 (EN); also elsewhere on the board
/ESP_IO0: R33.2; also elsewhere on the board
GND: C37.2, C38.2, R32.2, X1.2 (GND); also elsewhere on the board
unnamed: R33.1, X1.3 (OUT)

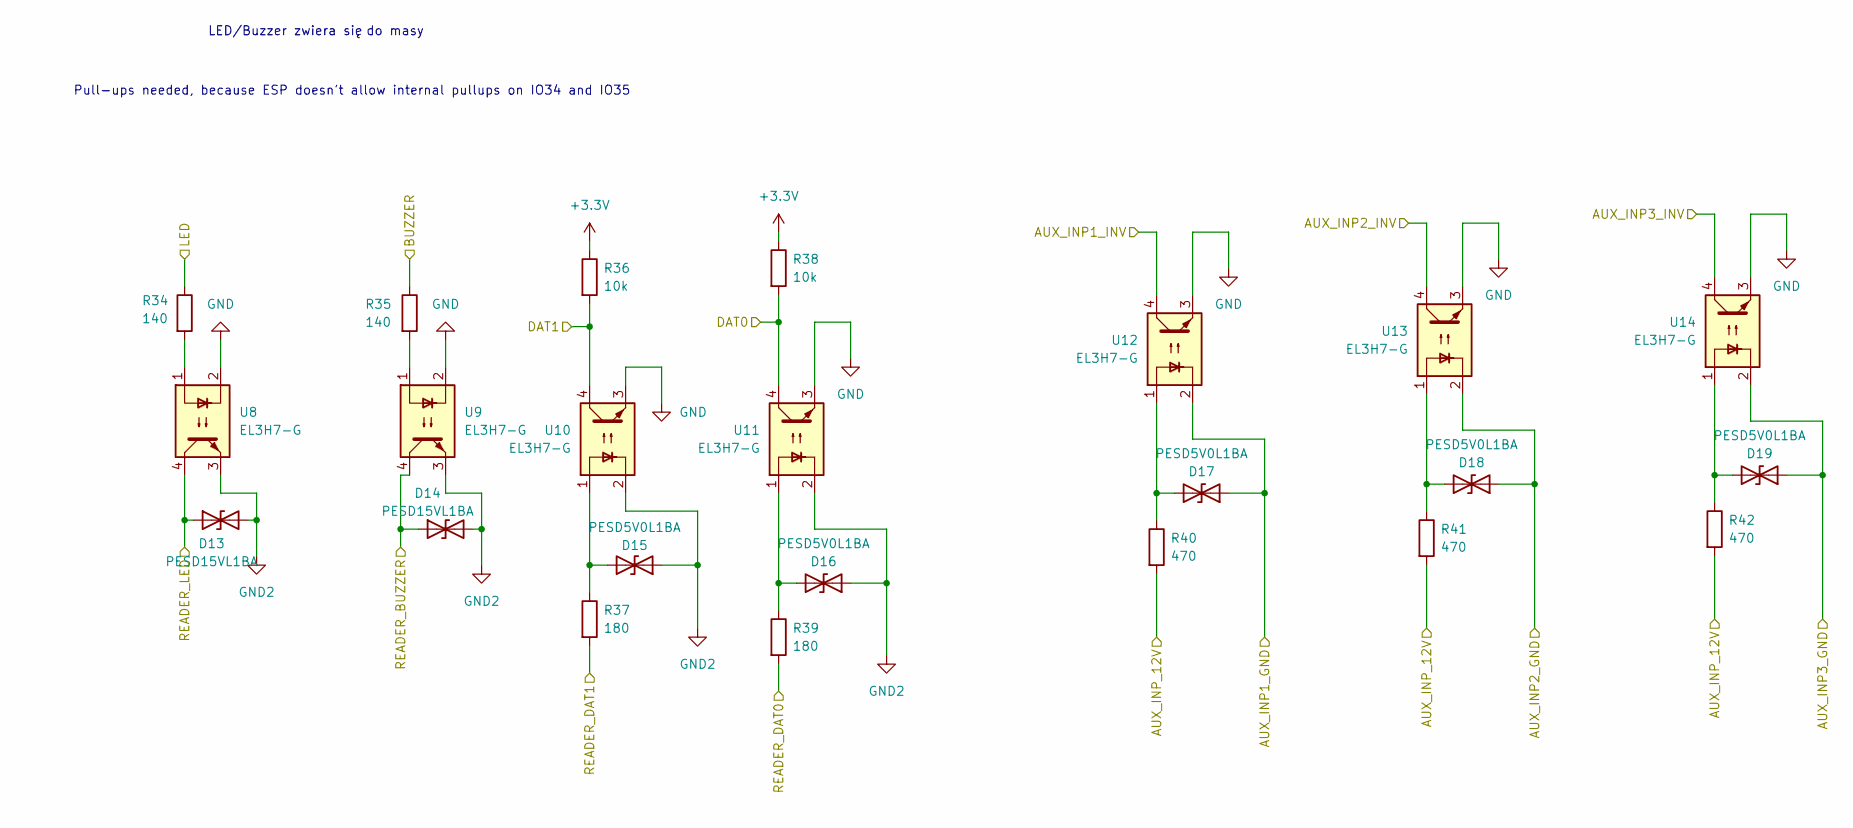
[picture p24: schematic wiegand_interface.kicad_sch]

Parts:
D13, D14: PESD15VL1BA; D_SOD-323; LCSC C18723438
D15, D16, D17, D18, D19: PESD5V0L1BA; D_SOD-323; LCSC C85380
R34, R35: 140; R_0603_1608Metric_Pad0.98x0.95mm_HandSolder; LCSC C2974027
R36, R38: 10k; R_0603_1608Metric_Pad0.98x0.95mm_HandSolder; LCSC C2930027
R37, R39: 180; R_0603_1608Metric_Pad0.98x0.95mm_HandSolder; LCSC C5140972
R40, R41, R42: 470; R_0603_1608Metric_Pad0.98x0.95mm_HandSolder; LCSC C2907172
U8, U9, U10, U11, U12, U13, U14: EL3H7-G; SSOP-4_4.4x2.6mm_P1.27mm; LCSC C92243

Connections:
+3.3V: R36.1, R38.1; also elsewhere on the board
/AUX_INP1_GND: D17.1 (A1), U12.2; also elsewhere on the board
/AUX_INP1_INV: U12.4; also elsewhere on the board
/AUX_INP2_GND: D18.1 (A1), U13.2; also elsewhere on the board
/AUX_INP2_INV: U13.4; also elsewhere on the board
/AUX_INP3_GND: D19.1 (A1), U14.2; also elsewhere on the board
/AUX_INP3_INV: U14.4; also elsewhere on the board
/BUZ_CTL: R35.1; also elsewhere on the board
/DAT0_INV: R38.2, U11.4; also elsewhere on the board
/DAT1_INV: R36.2, U10.4; also elsewhere on the board
/EXT_PWR: R40.2, R41.2, R42.2; also elsewhere on the board
/LED_CTL: R34.1; also elsewhere on the board
/READER_BUZZER: D14.1 (A1), U9.4; also elsewhere on the board
/READER_DAT0: R39.2; also elsewhere on the board
/READER_DAT1: R37.2; also elsewhere on the board
/READER_LED: D13.1 (A1), U8.4; also elsewhere on the board
GND: U8.2, U9.2, U10.3, U11.3, U12.3, U13.3, U14.3; also elsewhere on the board
GND2: D13.2 (A2), D14.2 (A2), D15.1 (A1), D16.1 (A1), U8.3, U9.3, U10.2, U11.2; also elsewhere on the board
unnamed: D15.2 (A2), R37.1, U10.1
unnamed: D16.2 (A2), R39.1, U11.1
unnamed: D17.2 (A2), R40.1, U12.1
unnamed: D18.2 (A2), R41.1, U13.1
unnamed: D19.2 (A2), R42.1, U14.1
unnamed: R34.2, U8.1
unnamed: R35.2, U9.1

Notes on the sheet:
LED/Buzzer zwiera się do masy
Pull-ups needed, because ESP doesn't allow internal pullups on IO34 and IO35

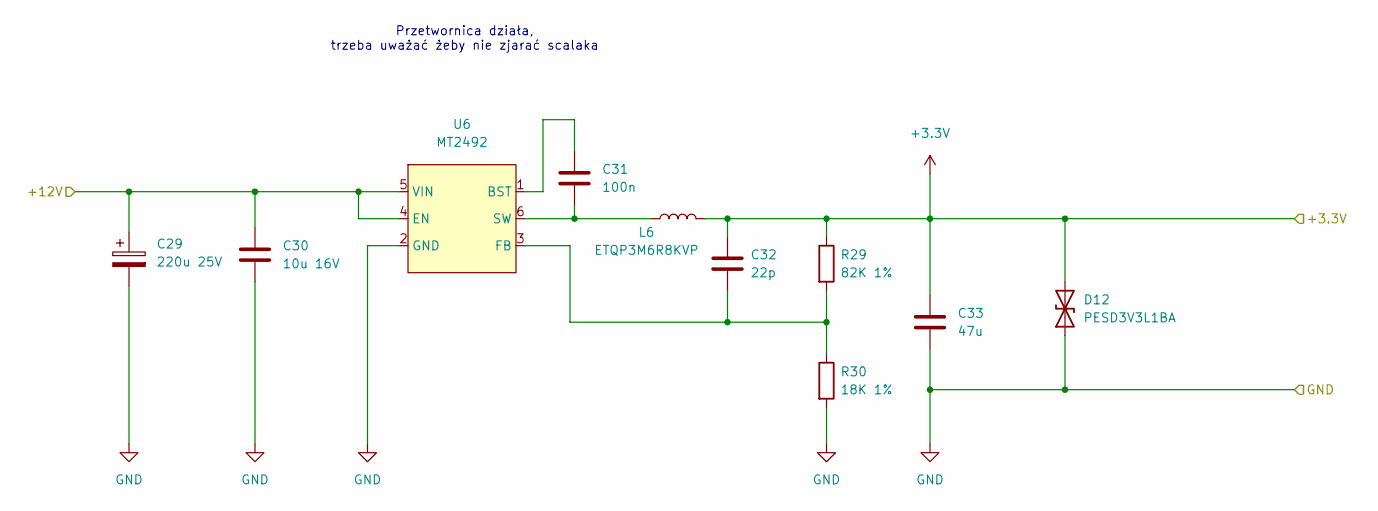
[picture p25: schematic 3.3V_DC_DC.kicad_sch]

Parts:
C29: 220u 25V; CP_Elec_6.3x7.7; LCSC C4747974
C30: 10u 16V; C_0603_1608Metric_Pad1.08x0.95mm_HandSolder; LCSC C92487
C31: 100n; C_0603_1608Metric_Pad1.08x0.95mm_HandSolder; LCSC C282519
C32: 22p; C_0603_1608Metric_Pad1.08x0.95mm_HandSolder; LCSC C376775
C33: 47u; C_0603_1608Metric_Pad1.08x0.95mm_HandSolder; LCSC C140782
D12: PESD3V3L1BA; D_SOD-323; LCSC C2687129
L6: ETQP3M6R8KVP; IND_PCC-M0530M-LP_PAN; LCSC C412311
R29: 82K 1%; R_0603_1608Metric_Pad0.98x0.95mm_HandSolder; LCSC C5140983
R30: 18K 1%; R_0603_1608Metric_Pad0.98x0.95mm_HandSolder; LCSC C2907001
U6: MT2492; SOT-23-6; LCSC C89358

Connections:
+3.3V: C32.1, C33.1, D12.2 (A2), L6.2, R29.1; also elsewhere on the board
+12V: C29.1, C30.1, U6.4 (EN), U6.5 (VIN); also elsewhere on the board
GND: C29.2, C30.2, C33.2, D12.1 (A1), R30.2, U6.2 (GND); also elsewhere on the board
unnamed: C31.1, U6.1 (BST)
unnamed: C32.2, R29.2, R30.1, U6.3 (FB)
unnamed: C31.2, L6.1, U6.6 (SW)

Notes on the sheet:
Przetwornica działa, trzeba uważać żeby nie zjarać scalaka

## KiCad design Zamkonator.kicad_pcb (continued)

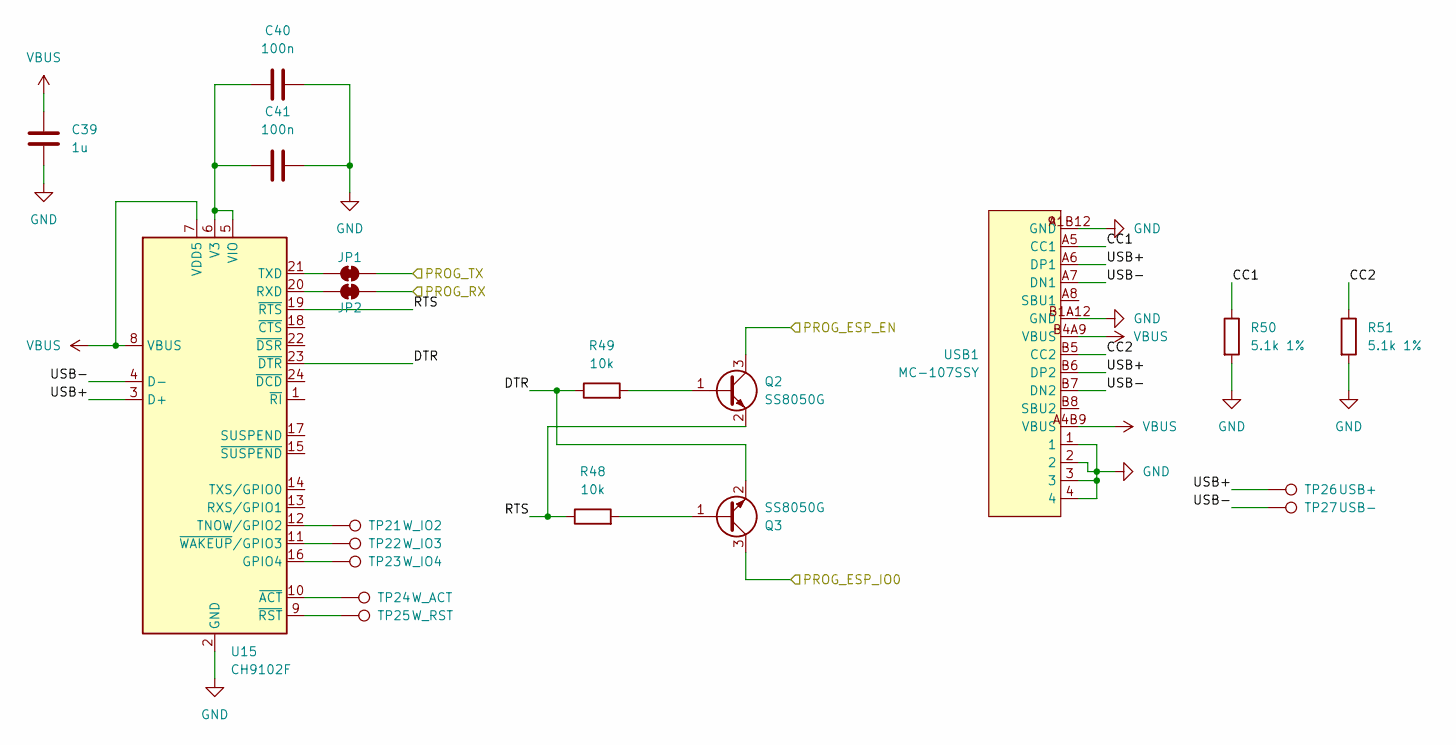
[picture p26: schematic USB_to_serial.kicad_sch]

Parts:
C39: 1u; C_0603_1608Metric; JLCPCB C559769
C40, C41: 100n; C_0603_1608Metric; JLCPCB C14663
JP1, JP2: SolderJumper_2_Bridged; SolderJumper-2_P1.3mm_Bridged_RoundedPad1.0x1.5mm
Q2, Q3: SS8050G; SOT-23; JLCPCB C164886
R48, R49: 10k; R_0603_1608Metric; JLCPCB C25804
R50, R51: 5.1k 1%; R_0603_1608Metric; JLCPCB C23186
TP21: W_IO2; TestPoint_Pad_D1.0mm
TP22: W_IO3; TestPoint_Pad_D1.0mm
TP23: W_IO4; TestPoint_Pad_D1.0mm
TP24: W_ACT; TestPoint_Pad_D1.0mm
TP25: W_RST; TestPoint_Pad_D1.0mm
TP26: USB+; TestPoint_Pad_D1.0mm
TP27: USB-; TestPoint_Pad_D1.0mm
U15: CH9102F; QFN-24-1EP_4x4mm_P0.5mm_EP2.6x2.6mm; JLCPCB C2858418
USB1: MC-107SSY; USB-TYPE-C-SMD_MC-107SSY; JLCPCB C3039307

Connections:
/ESP_EN: Q2.3 (C); also elsewhere on the board
/ESP_RX: JP1.2 (B); also elsewhere on the board
/ESP_TX: JP2.2 (B); also elsewhere on the board
/USB_to_serial/CC1: R50.1, USB1.A5 (CC1)
/USB_to_serial/CC2: R51.1, USB1.B5 (CC2)
/USB_to_serial/DTR: Q3.2 (E), R49.1, U15.23 (~DTR)
/USB_to_serial/PROG_ESP_IO0: Q3.3 (C); also elsewhere on the board
/USB_to_serial/RTS: Q2.2 (E), R48.1, U15.19 (~RTS)
/USB_to_serial/USB+: TP26.1 (1_1), U15.3 (D+), USB1.A6 (DP1), USB1.B6 (DP2)
/USB_to_serial/USB-: TP27.1 (1_1), U15.4 (D-), USB1.A7 (DN1), USB1.B7 (DN2)
GND: C39.1, C40.2, C41.2, R50.2, R51.2, U15.2 (GND), U15.25 (GND), USB1.1, USB1.2, USB1.3, USB1.4, USB1.A1B12 (GND), USB1.B1A12 (GND); also elsewhere on the board
unnamed: JP1.1 (A), U15.21 (TXD)
unnamed: JP2.1 (A), U15.20 (RXD)
unnamed: Q2.1 (B), R49.2
unnamed: Q3.1 (B), R48.2
unnamed: TP23.1 (1_1), U15.16 (GPIO4)
unnamed: TP21.1 (1_1), U15.12 (TNOW/GPIO2)
unnamed: C40.1, C41.1, U15.5 (VIO), U15.6 (V3)
unnamed: TP24.1 (1_1), U15.10 (~ACT)
unnamed: TP25.1 (1_1), U15.9 (~RST)
unnamed: TP22.1 (1_1), U15.11 (~WAKEUP/GPIO3)
VBUS: C39.2, U15.7 (VDD5), U15.8 (VBUS), USB1.A4B9 (VBUS), USB1.B4A9 (VBUS)

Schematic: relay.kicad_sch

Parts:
D20: 1N4007; D_SMA_Handsoldering; LCSC C7528875
K1: SRD-DC3V-SL-C; Relay_SPDT_SANYOU_SRD_Series_Form_C; LCSC C688864
Q1: DMG2302U; SOT-23; LCSC C460977
R43: 100K 1%; R_0603_1608Metric_Pad0.98x0.95mm_HandSolder; LCSC C2906980
R44: 1k; R_0603_1608Metric_Pad0.98x0.95mm_HandSolder; LCSC C22548

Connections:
+3.3V: D20.1 (K), K1.2; also elsewhere on the board
/RELAY_CTL: R43.1, R44.1; also elsewhere on the board
/R_C: K1.1; also elsewhere on the board
/R_NC: K1.4; also elsewhere on the board
/R_NO: K1.3; also elsewhere on the board
GND: Q1.2 (S), R43.2; also elsewhere on the board
unnamed: D20.2 (A), K1.5, Q1.3 (D)
unnamed: Q1.1 (G), R44.2

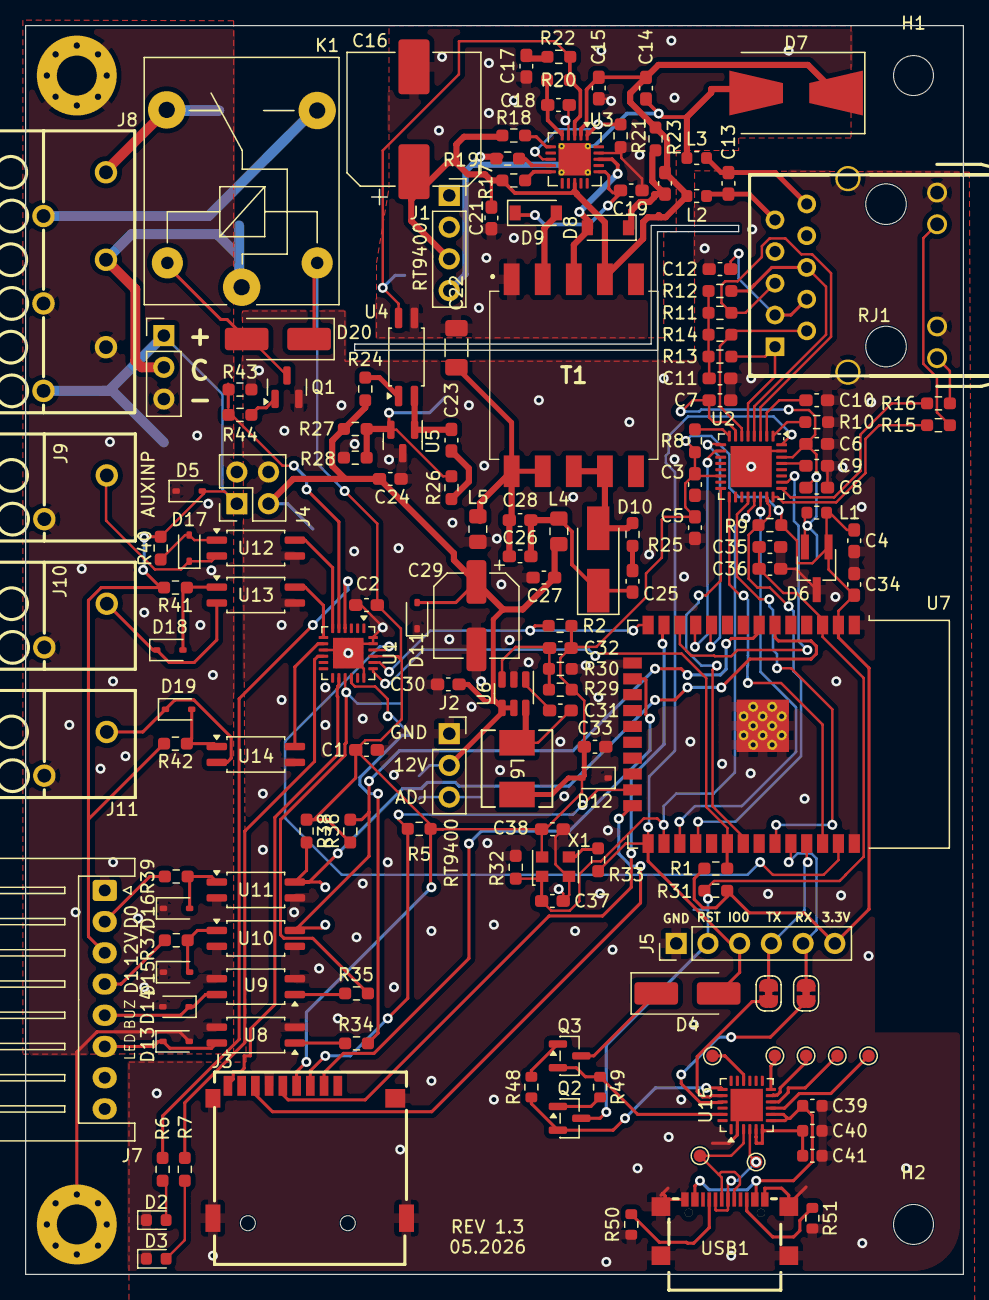
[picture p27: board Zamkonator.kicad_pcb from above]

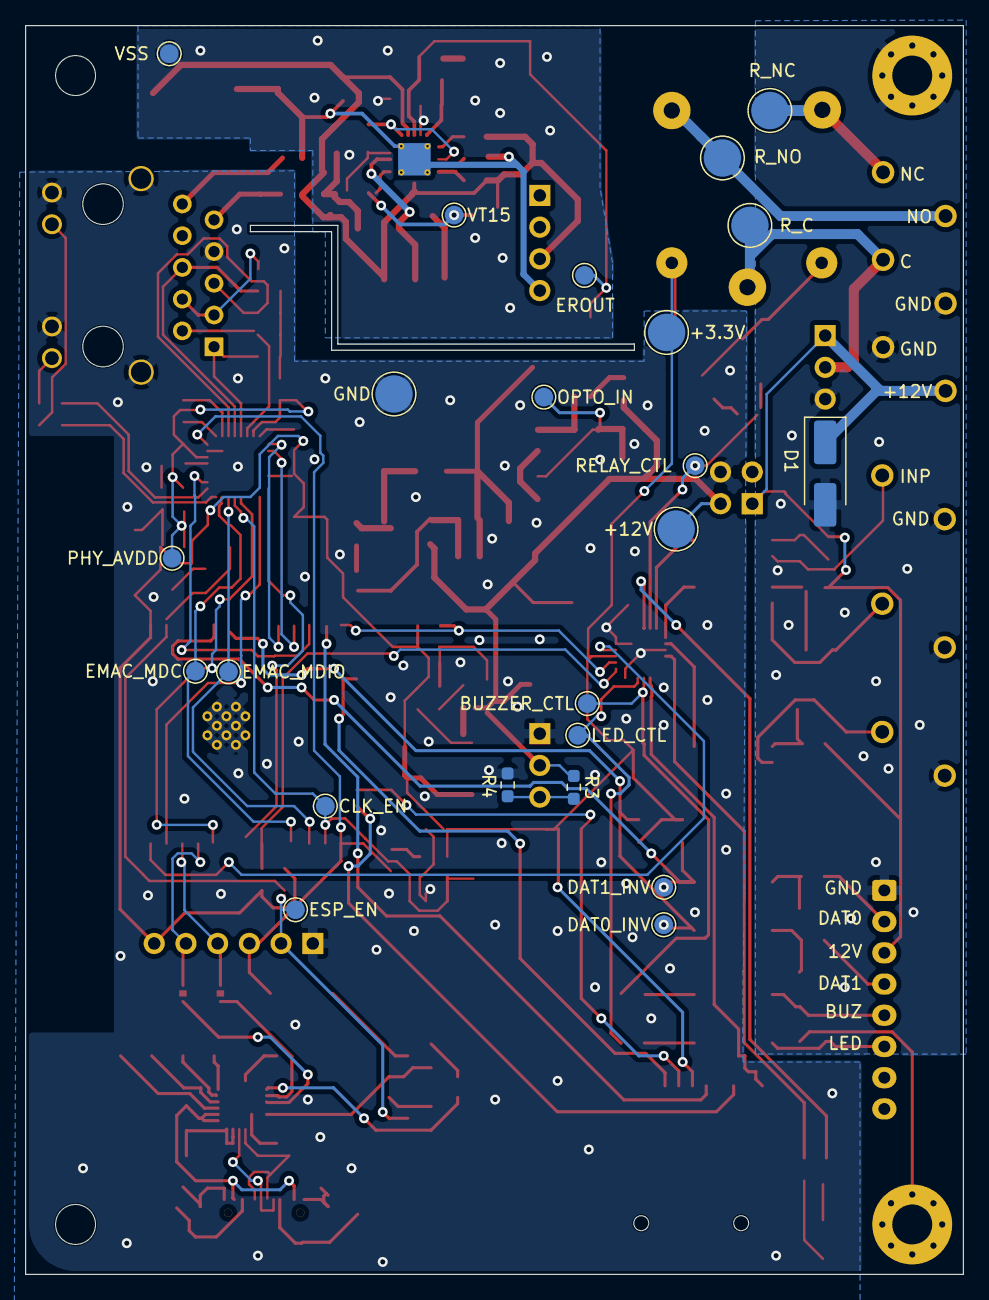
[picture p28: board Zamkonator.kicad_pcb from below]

Board: 2 copper layers, 75.1 x 100.0 mm, 182 parts (23 on the bottom side), 119 nets.

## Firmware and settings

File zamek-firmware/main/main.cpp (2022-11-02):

#include <stdio.h>
#include "sdkconfig.h"
#include "freertos/FreeRTOS.h"
#include "freertos/task.h"
#include "esp_chip_info.h"
#include "esp_flash.h"
#include "main.h"
#include "esp_littlefs.h"
#include "esp_err.h"
#include "esp_log.h"
#include "esp_system.h"
#include "nvs_flash.h"
#include <memory>

#include "Storage.h"

#define TAG "main"

static void initialize_littlefs();
static void initialize_nvs();

void app_main(void)
{
    initialize_nvs();
    initialize_littlefs();

    std::unique_ptr<App> app = std::make_unique<App>();
    app->run();
}

static void initialize_littlefs()
{
    esp_vfs_littlefs_conf_t conf = {
        .base_path = Storage::FS_MOUNT_POINT,
        .partition_label = "littlefs",
        .format_if_mount_failed = true,
        .dont_mount = false,
    };

    // Use settings defined above to initialize and mount LittleFS filesystem.
    // Note: esp_vfs_littlefs_register is an all-in-one convenience function.
    esp_err_t ret = esp_vfs_littlefs_register(&conf);

    if (ret != ESP_OK)
    {
        if (ret == ESP_FAIL)
        {
            ESP_LOGE(TAG, "Failed to mount or format filesystem");
        }
        else if (ret == ESP_ERR_NOT_FOUND)
        {
            ESP_LOGE(TAG, "Failed to find LittleFS partition");
        }
        else
        {
            ESP_LOGE(TAG, "Failed to initialize LittleFS (%s)", esp_err_to_name(ret));
        }
        return;
    }
    ESP_LOGI(TAG, "LittleFS initialized, listing files");
    auto files = Storage::listFiles(Storage::FS_MOUNT_POINT);
    ESP_LOGI(TAG, "Found %d files", files.size());
    for (auto file : files)
    {
        ESP_LOGI(TAG, "File: %s", file.c_str());
    }
}
/**
 * @brief Initialize NVS for calibration data
 * 
 */
static void initialize_nvs()
{
    // Initialize NVS
    esp_err_t ret = nvs_flash_init();
    if (ret == ESP_ERR_NVS_NO_FREE_PAGES || ret == ESP_ERR_NVS_NEW_VERSION_FOUND)
    {
        ESP_ERROR_CHECK(nvs_flash_erase());
        ret = nvs_flash_init();
    }
    ESP_ERROR_CHECK(ret);
}

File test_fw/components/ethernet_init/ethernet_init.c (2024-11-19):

/*
 * SPDX-FileCopyrightText: 2022-2024 Espressif Systems (Shanghai) CO LTD
 *
 * SPDX-License-Identifier: Unlicense OR CC0-1.0
 */
#include "ethernet_init.h"
#include "esp_log.h"
#include "esp_check.h"
#include "esp_mac.h"
#include "driver/gpio.h"
#include "sdkconfig.h"
#if CONFIG_EXAMPLE_USE_SPI_ETHERNET
#include "driver/spi_master.h"
#endif // CONFIG_EXAMPLE_USE_SPI_ETHERNET

#if CONFIG_EXAMPLE_SPI_ETHERNETS_NUM
#define SPI_ETHERNETS_NUM           CONFIG_EXAMPLE_SPI_ETHERNETS_NUM
#else
#define SPI_ETHERNETS_NUM           0
#endif

#if CONFIG_EXAMPLE_USE_INTERNAL_ETHERNET
#define INTERNAL_ETHERNETS_NUM      1
#else
#define INTERNAL_ETHERNETS_NUM      0
#endif

#define INIT_SPI_ETH_MODULE_CONFIG(eth_module_config, num)                                      \
    do {                                                                                        \
        eth_module_config[num].spi_cs_gpio = CONFIG_EXAMPLE_ETH_SPI_CS ##num## _GPIO;           \
        eth_module_config[num].int_gpio = CONFIG_EXAMPLE_ETH_SPI_INT ##num## _GPIO;             \
        eth_module_config[num].polling_ms = CONFIG_EXAMPLE_ETH_SPI_POLLING ##num## _MS;         \
        eth_module_config[num].phy_reset_gpio = CONFIG_EXAMPLE_ETH_SPI_PHY_RST ##num## _GPIO;   \
        eth_module_config[num].phy_addr = CONFIG_EXAMPLE_ETH_SPI_PHY_ADDR ##num;                \
    } while(0)

typedef struct {
    uint8_t spi_cs_gpio;
    int8_t int_gpio;
    uint32_t polling_ms;
    int8_t phy_reset_gpio;
    uint8_t phy_addr;
    uint8_t *mac_addr;
}spi_eth_module_config_t;

static const char *TAG = "example_eth_init";
#if CONFIG_EXAMPLE_USE_SPI_ETHERNET
static bool gpio_isr_svc_init_by_eth = false; // indicates that we initialized the GPIO ISR service
#endif // CONFIG_EXAMPLE_USE_SPI_ETHERNET


#if CONFIG_EXAMPLE_USE_INTERNAL_ETHERNET
/**
 * @brief Internal ESP32 Ethernet initialization
 *
 * @param[out] mac_out optionally returns Ethernet MAC object
 * @param[out] phy_out optionally returns Ethernet PHY object
 * @return
 *          - esp_eth_handle_t if init succeeded
 *          - NULL if init failed
 */
static esp_eth_handle_t eth_init_internal(esp_eth_mac_t **mac_out, esp_eth_phy_t **phy_out)
{
    esp_eth_handle_t ret = NULL;

    // Init common MAC and PHY configs to default
    eth_mac_config_t mac_config = ETH_MAC_DEFAULT_CONFIG();
    eth_phy_config_t phy_config = ETH_PHY_DEFAULT_CONFIG();

    // Update PHY config based on board specific configuration
    phy_config.phy_addr = CONFIG_EXAMPLE_ETH_PHY_ADDR;
    phy_config.reset_gpio_num = CONFIG_EXAMPLE_ETH_PHY_RST_GPIO;
    phy_config.reset_timeout_ms = 1000;
    // Init vendor specific MAC config to default
    eth_esp32_emac_config_t esp32_emac_config = ETH_ESP32_EMAC_DEFAULT_CONFIG();
    // Update vendor specific MAC config based on board configuration
    esp32_emac_config.smi_gpio.mdc_num = CONFIG_EXAMPLE_ETH_MDC_GPIO;
    esp32_emac_config.smi_gpio.mdio_num = CONFIG_EXAMPLE_ETH_MDIO_GPIO;
#if CONFIG_EXAMPLE_USE_SPI_ETHERNET
    // The DMA is shared resource between EMAC and the SPI. Therefore, adjust
    // EMAC DMA burst length when SPI Ethernet is used along with EMAC.
    esp32_emac_config.dma_burst_len = ETH_DMA_BURST_LEN_4;
#endif // CONFIG_EXAMPLE_USE_SPI_ETHERNET
    // Create new ESP32 Ethernet MAC instance
    esp_eth_mac_t *mac = esp_eth_mac_new_esp32(&esp32_emac_config, &mac_config);
    // Create new PHY instance based on board configuration
#if CONFIG_EXAMPLE_ETH_PHY_IP101
    esp_eth_phy_t *phy = esp_eth_phy_new_ip101(&phy_config);
#elif CONFIG_EXAMPLE_ETH_PHY_RTL8201
    esp_eth_phy_t *phy = esp_eth_phy_new_rtl8201(&phy_config);
#elif CONFIG_EXAMPLE_ETH_PHY_LAN87XX
    esp_eth_phy_t *phy = esp_eth_phy_new_lan87xx(&phy_config);
#elif CONFIG_EXAMPLE_ETH_PHY_DP83848
    esp_eth_phy_t *phy = esp_eth_phy_new_dp83848(&phy_config);
#elif CONFIG_EXAMPLE_ETH_PHY_KSZ80XX
    esp_eth_phy_t *phy = esp_eth_phy_new_ksz80xx(&phy_config);
#endif
    // Init Ethernet driver to default and install it
    esp_eth_handle_t eth_handle = NULL;
    esp_eth_config_t config = ETH_DEFAULT_CONFIG(mac, phy);
    ESP_GOTO_ON_FALSE(esp_eth_driver_install(&config, &eth_handle) == ESP_OK, NULL,
                        err, TAG, "Ethernet driver install failed");

    if (mac_out != NULL) {
        *mac_out = mac;
    }
    if (phy_out != NULL) {
        *phy_out = phy;
    }
    return eth_handle;
err:
    if (eth_handle != NULL) {
        esp_eth_driver_uninstall(eth_handle);
    }
    if (mac != NULL) {
        mac->del(mac);
    }
    if (phy != NULL) {
        phy->del(phy);
    }
    return ret;
}
#endif // CONFIG_EXAMPLE_USE_INTERNAL_ETHERNET

#if CONFIG_EXAMPLE_USE_SPI_ETHERNET
/**
 * @brief SPI bus initialization (to be used by Ethernet SPI modules)
 *
 * @return
 *          - ESP_OK on success
 */
static esp_err_t spi_bus_init(void)
{
    esp_err_t ret = ESP_OK;

#if (CONFIG_EXAMPLE_ETH_SPI_INT0_GPIO >= 0) || (CONFIG_EXAMPLE_ETH_SPI_INT1_GPIO > 0)
    // Install GPIO ISR handler to be able to service SPI Eth modules interrupts
    ret = gpio_install_isr_service(0);
    if (ret == ESP_OK) {
        gpio_isr_svc_init_by_eth = true;
    } else if (ret == ESP_ERR_INVALID_STATE) {
        ESP_LOGW(TAG, "GPIO ISR handler has been already installed");
        ret = ESP_OK; // ISR handler has been already installed so no issues
    } else {
        ESP_LOGE(TAG, "GPIO ISR handler install failed");
        goto err;
    }
#endif

    // Init SPI bus
    spi_bus_config_t buscfg = {
        .miso_io_num = CONFIG_EXAMPLE_ETH_SPI_MISO_GPIO,
        .mosi_io_num = CONFIG_EXAMPLE_ETH_SPI_MOSI_GPIO,
        .sclk_io_num = CONFIG_EXAMPLE_ETH_SPI_SCLK_GPIO,
        .quadwp_io_num = -1,
        .quadhd_io_num = -1,
    };
    ESP_GOTO_ON_ERROR(spi_bus_initialize(CONFIG_EXAMPLE_ETH_SPI_HOST, &buscfg, SPI_DMA_CH_AUTO),
                        err, TAG, "SPI host #%d init failed", CONFIG_EXAMPLE_ETH_SPI_HOST);

err:
    return ret;
}
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

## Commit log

2022-10-18 finish shcematic
    [3.3V_DC_DC.kicad_sch, CLOCK.kicad_sch, ESP32.kicad_sch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]
2022-10-23 feat: add more LCSC symbols
    [ESP32.kicad_sch, Zamkonator.kicad_sch, ethernet_phy.kicad_sch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]
2022-10-23 Remove non-standard resistor
    [Zamkonator.kicad_sch, wiegand_interface.kicad_sch]
2022-10-27 fixup wrong resistor values
    [Zamkonator.kicad_sch, wiegand_interface.kicad_sch]
2022-11-02 Add basic spifs structure
    [partitions.csv]
2022-12-05 Add some more footprints
    [Zamkonator.kicad_sch, ethernet_phy.kicad_sch, poe_psu.kicad_sch]
2023-01-14 Add even more footprints
    [3.3V_DC_DC.kicad_sch, Zamkonator.kicad_sch, poe_psu.kicad_sch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]
2023-01-15 basic ETH layout
    [3.3V_DC_DC.kicad_sch, CLOCK.kicad_sch, TSX-3225_16.0000MF18X-AC3.step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]
2023-02-01 layout fixes
    [3.3V_DC_DC.kicad_sch, CLOCK.kicad_sch, Zamkonator.kicad_pcb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]
2023-02-10 Finish basic layout
    [Zamkonator.kicad_pcb, Zamkonator.kicad_sch]
2023-02-10 add screw holes
    [Zamkonator.kicad_pcb, Zamkonator.kicad_sch]
2023-02-11 More tracks, before big change in layout...
    [Zamkonator.kicad_pcb]
2023-02-12 Finish layout
    [ESP32.kicad_sch, Zamkonator.kicad_pcb, Zamkonator.kicad_sch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]
2023-02-12 add header labels
    [Zamkonator.kicad_pcb]
2023-02-13 Add testpoints, jumpers
    [ESP32.kicad_sch, Zamkonator.kicad_pcb, Zamkonator.kicad_sch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]
2023-02-13 Update inductor footprint
    [Zamkonator.kicad_pcb]
2023-02-13 RT9400 module option added
    [Zamkonator.kicad_pcb, Zamkonator.kicad_sch, ethernet_phy.kicad_sch]
2023-02-13 Finishing touches, rounded PCB
    [Zamkonator.kicad_pcb]
2023-02-13 adjust silkscreen
    [Zamkonator.kicad_pcb]
2023-02-13 Fixup diode footprint and add more LCSC numbers
    [Zamkonator.kicad_pcb, Zamkonator.kicad_sch, ethernet_phy.kicad_sch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]
2023-02-14 Add more LCSC markings, change to electrolytic caps :
    [3.3V_DC_DC.kicad_sch, CLOCK.kicad_sch, ESP32.kicad_sch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]
2023-02-15 Switch to LCSC RJ45 socket
    [Zamkonator.kicad_pcb, Zamkonator.kicad_sch, ethernet_phy.kicad_sch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]
2023-02-17 Add missing files
    [Zamkonator.csv]
2023-03-06 Silkscreen fixes
    [Zamkonator.kicad_pcb]
2023-03-19 Add stuff
    [Zamkonator-B_Cu.gbr, Zamkonator-B_Mask.gbr, Zamkonator-B_Paste.gbr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]
2024-10-31 Update kicad files
    [3.3V_DC_DC.kicad_sch, CLOCK.kicad_sch, ESP32.kicad_sch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]
2024-11-19 Increaste timeout, add wait before reboot
    [ethernet_init.c]
2024-11-20 Kicad updates, added missing resistances
    [3.3V_DC_DC.kicad_sch, CLOCK.kicad_sch, ESP32.kicad_sch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]
2024-11-22 Update schematic for V1.1
    [3.3V_DC_DC.kicad_sch, CLOCK.kicad_sch, ESP32.kicad_sch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]
2024-12-29 use contributed symbol for RTL8021F
    [Zamkonator.kicad_pcb, ethernet_phy.kicad_sch]
2025-09-05 BOM updates & schematic fixes
    [3.3V_DC_DC.kicad_sch, CLOCK.kicad_sch, ESP32.kicad_sch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]
2025-09-28 fix PoE transofrmer polarity, add more relay outputs
    [Zamkonator.kicad_sch, poe_psu.kicad_sch, wiegand_interface.kicad_sch]
2025-10-03 DO the bulk of rev 1.2 layout
    [3.3V_DC_DC.kicad_sch, CLOCK.kicad_sch, Zamkonator.kicad_pcb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]
2025-10-03 Cleanup footprints
    [TF-SMD_XKTF-N02-N.step]
2025-10-03 Use kicad symbol for the optotransistor
    [3.3V_DC_DC.kicad_sch, CLOCK.kicad_sch, ethernet_phy.kicad_sch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]
2025-10-03 Remove custom library for EL3H7, use the kicad one.
    [Zamkonator.kicad_pcb, poe_psu.kicad_sch, wiegand_interface.kicad_sch]
2025-10-03 Use kicad built-in symbol for AN431.
    [poe_psu.kicad_sch]
2025-10-03 remove custom footprint for Si3404
    [Zamkonator.kicad_pcb, poe_psu.kicad_sch]
2025-10-03 Update crystal LCSC number, use built-in footprint
    [CLOCK.kicad_sch, Zamkonator.kicad_pcb]
2025-10-03 remove custom oscillator symbol, add 3d model
    [Oscillator_3225.step, Zamkonator.kicad_pcb]
2025-10-03 Add optocoupler 3d model
    [SSOP-4.STEP, Zamkonator.kicad_pcb]
2025-10-03 Add PoE transformer 3D model
    [RJ45-TH_HY931147C.step, XFMR-SMD_10P-L13.5-W13.5-H12.3-P2.48-LS17.7-BR.step, Zamkonator.kicad_pcb]
2025-10-03 Use cheaper SD card socket
    [Zamkonator.kicad_pcb, Zamkonator.kicad_sch]
2025-10-03 Add all missing 3D models
    [IND-SMD_L5.5-W5.0-H3.0_ETQP4M220YFP.step, Zamkonator.kicad_pcb]
2025-10-04 Prepare push in connectors, add aux input
    [CONN-TH_KF236-5.0-5P.step, CONN-TH_KF236-5.0-6P.step, Zamkonator.kicad_pcb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]
2025-10-06 try playing around with the output screw terminals
    [Zamkonator.kicad_sch, wiegand_interface.kicad_sch]
2025-10-08 Finish the schematic maybe
    [CONN-TH_250-202.step, CONN-TH_250-206.step, CONN-TH_KF236-5.0-5P.step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]
2025-10-08 Finish preliminary routing
    [Zamkonator.kicad_pcb, Zamkonator.kicad_sch, poe_psu.kicad_sch]
2025-10-08 Finish routing
    [Zamkonator.kicad_pcb, Zamkonator.kicad_sch, ethernet_phy.kicad_sch]
2026-03-25 BOM updates
    [3.3V_DC_DC.kicad_sch, CLOCK.kicad_sch, ESP32.kicad_sch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]
2026-05-09 misc updates, extend board
    [Zamkonator.kicad_pcb, Zamkonator.kicad_sch, wiegand_interface.kicad_sch]
2026-05-26 Zamkonator rev 1.3
    [3.3V_DC_DC.kicad_sch, CLOCK.kicad_sch, ESP32.kicad_sch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]
2026-06-29 Rev 1.3, BOM optimizations
    [3.3V_DC_DC.kicad_sch, CLOCK.kicad_sch, ESP32.kicad_sch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]
